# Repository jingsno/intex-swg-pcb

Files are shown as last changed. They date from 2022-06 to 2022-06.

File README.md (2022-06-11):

# Intex SWG automaton

This is a PCB for Intex SWG Automation at
https://github.com/tonyflores1006/intex-swg-iot

Discussion here
https://www.troublefreepool.com/threads/automation-of-intex-swg.228606/

This PCB is suitable for both the TM1650 and the PIC16F88 version of the display board.

Software for the "non TM1650" (18 pin) version of the display board is under development.
(Current status of non released development version of the software, allows for fullt control of the Intex SWG from a web interface.)

Known models without the TM1650 chip:
* Intex Krystal Clear salt water system® ECO 6220 / CG-26670 (7-led/5 buttons), Max 56800 Liters

*PCB for Intex SWG automation*
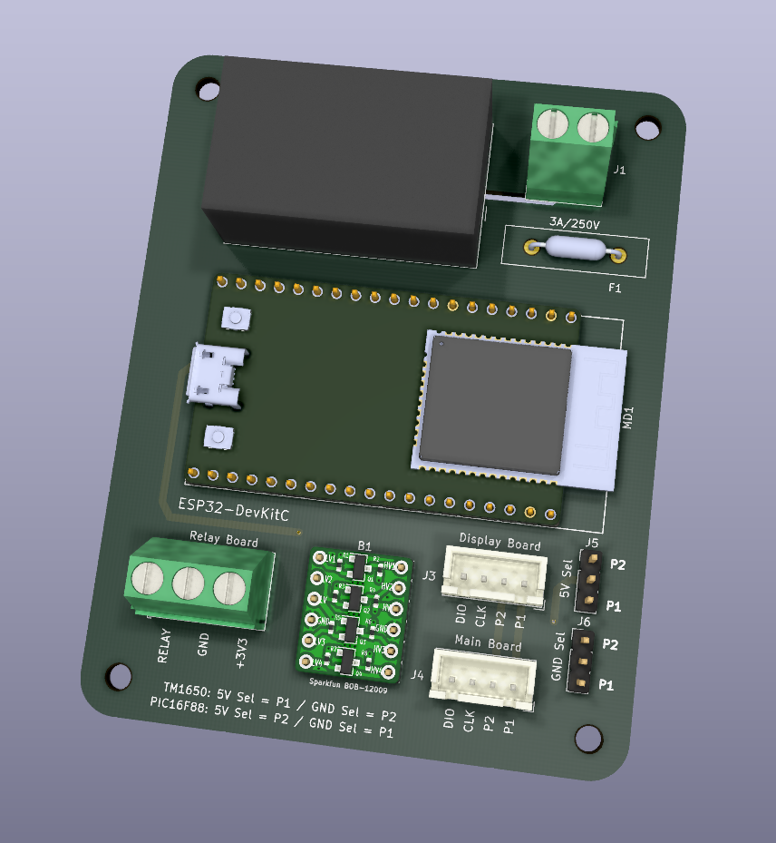
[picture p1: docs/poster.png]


## Schematic

Link to [PDF Schematic](docs/intex-swg-pcb.pdf)

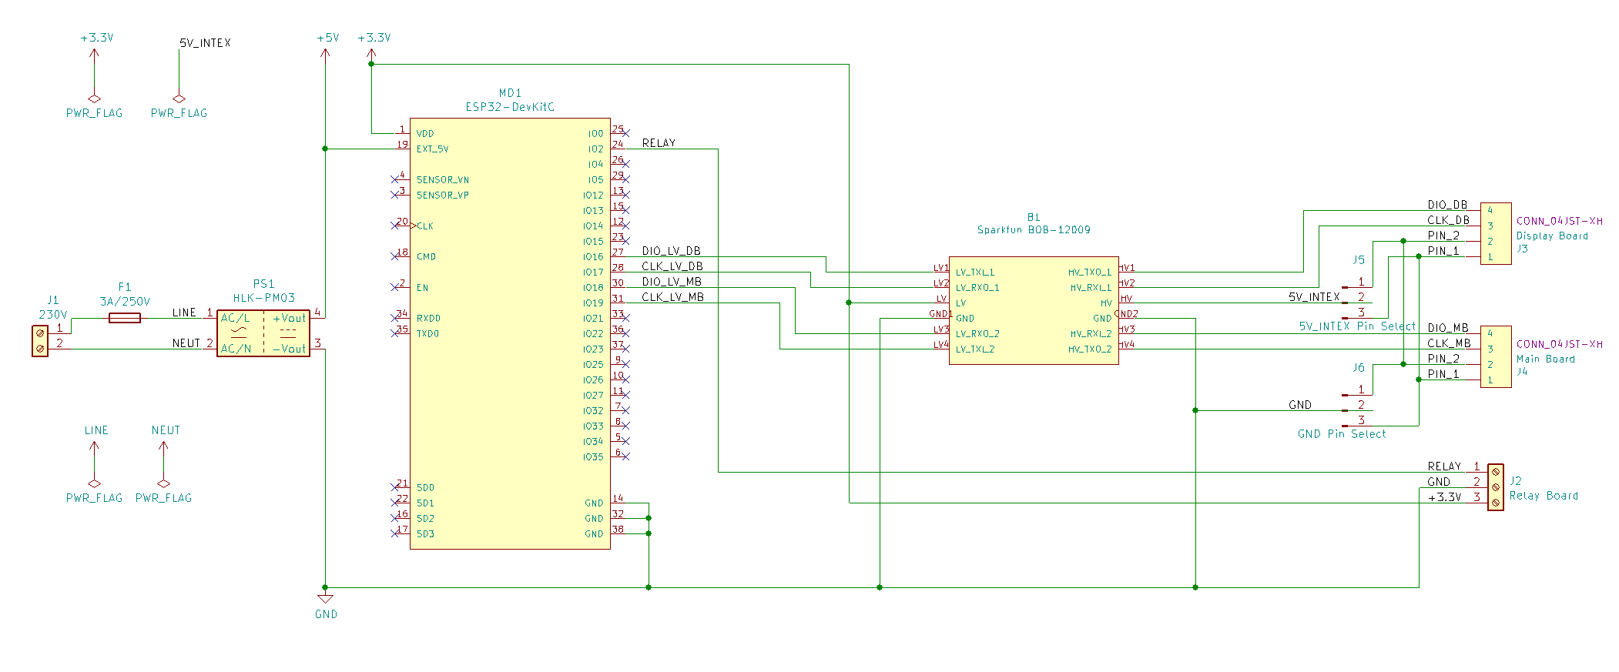
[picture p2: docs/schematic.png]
Schematic


## Parts list

| Part | |
|---|---|
| ESP32-DevkitC ext antenna |  https://www.digikey.com/en/products/detail/espressif-systems/ESP32-DEVKITC-32U/9357002 | 
| IRM-03-5 | https://www.digikey.com/en/products/detail/mean-well-usa-inc/IRM-03-5/7704640 |
| Level shifter to/from 5V/3.3V | https://www.aliexpress.com/item/1005001621978054.html | 
| 3.3V Relay module | https://www.aliexpress.com/item/32884967707.html | 
| 2x Female and 1x Male XH2.54 4pin connectors | https://www.aliexpress.com/item/4000126563819.html | 
| Stepper Motor cables/wire XH2.54 4pin | https://www.aliexpress.com/item/1005001361294507.html |
| Fuse 3A / 250V | https://www.aliexpress.com/item/32702176964.html | 
| 2-pin screw terminal | https://www.aliexpress.com/item/1005002971443405.html  | 
| 3-pin screw terminal | https://www.aliexpress.com/item/1005002971443405.html  | 
| 2x 3-pin header with jumper (or wire) | https://www.aliexpress.com/item/32873263301.html  |

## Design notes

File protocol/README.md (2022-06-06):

# Intex SWG (without TM1650 LED driver) protocol

Some Intex SWG models do not contain the TM1650 LED driver chip
This document contians the protocol for the communication between the Main/Displayboard for these models.

Discussion here
https://www.troublefreepool.com/threads/automation-of-intex-swg.228606/

Known models without the TM1650 chip:
* Intex Krystal Clear salt water system® ECO 6220 / CG-26670 (7-led/5 buttons), Max 56800 Liters

## General signal information

---
#### Note:  The information below is based on the asumption that the encodig is done with a high pulse. This is for decoding purposes. It might also be possible to consider the encoding scheme as "Short-Low,Long-High" as "one. and "Short-Low, Short-High" as Zero. Or alternativly as "Long-High,Short-Low" as "one. and "Short-High,Short-Low, " as Zero

* Starts with a Low 200 μS pulse
* Long High 800 μS for "one", followed by a Low 200 μS pulse as "spacer" 
* Short High 200 μS for "zero", followed by a Low 200 μS pulse as "spacer" 
* Ends with returning to high

---

The communication from the displayboard to the main board (buttons), uses the line marked as "CLK"  
*ESP32: IO17 input from display board, IO19 output to mainboard*

The communication from the main board to the displayboard (7-segment and LEDs), uses the line marked as "DIO"  
*ESP32: IO18 input from main board, IO16 output to displayboard*  

The data lines is normally high  
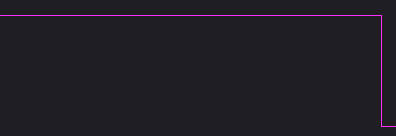
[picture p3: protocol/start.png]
  

A "one" is a long high pulse with the following characteristics:  
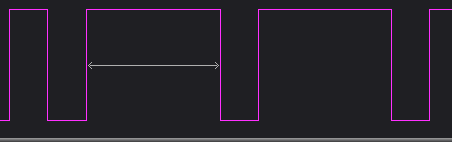
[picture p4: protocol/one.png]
  
Long High 800 μS

A "zero" is a short high pulse with the following characteristics:  
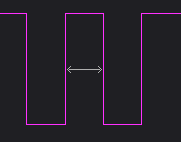
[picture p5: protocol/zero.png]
  
Short High 200 μS

Inbetween the data signals, there is a short low 200μS  
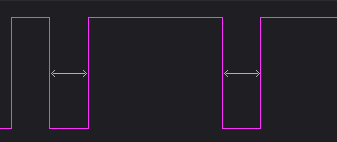
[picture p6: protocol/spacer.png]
  
Short Low 200 μS

The transmission ends with a Short Low of 200μS  
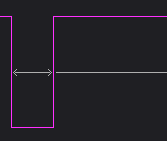
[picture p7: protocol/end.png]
  

## Communication from display board (buttons) to main board

The data from the buttons to the main board consists of two 8 bit values (bytes), where the second byte is the inverted of the first byte

The buttons is arranged in as a "plus", with a center button. They are named N, S, E, W, and C in the following table
~~~
             
             N SCEW  Button pressed  
1111 1011 0000 0100  C 
1111 1101 0000 0010  E 
1111 1110 0000 0001  W 
1110 1111 0001 0000  N 
1111 0111 0000 1000  S 
1111 1100 0000 0011  EW
1110 0111 0001 1000  NS
1110 1110 0001 0001  WN
1111 0110 0000 1001  WS
1110 1101 0001 0010  EN
1111 0101 0000 1010  ES
1111 1111 0000 0000  Release Buttons
---- ---- 
Inverted
of second
byte
~~~

*Example*
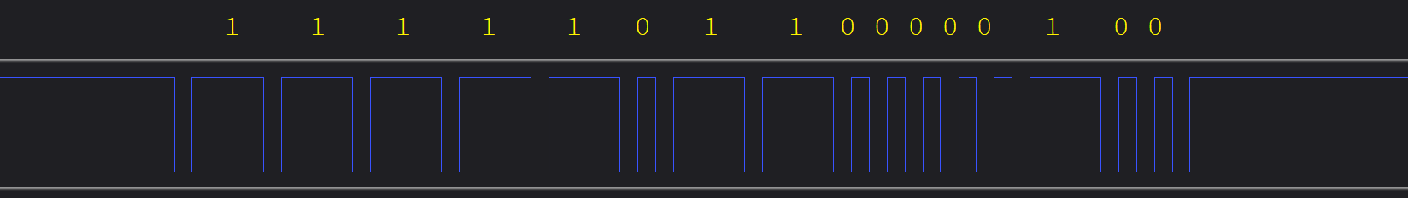
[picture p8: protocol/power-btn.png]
 
*C-button (Power) is pressed*

When the buttons are released the display board transmits
~~~
1111 1111 0000 0000
~~~

On the CG-26670 model, the buttons coresponds to:

N = Boost  
S = Self-Clean  
W = Lock/Unlock  
E = Timer  
C = Power  

## Communication from the main board to display board (7-segment and LEDs)

The data from the main board to the display board (7-segments/and LEDs), consists of a 32 bit value.
The first 16 bits is used for the two 7-segment displays, the last 16 bits for LEDs and status.

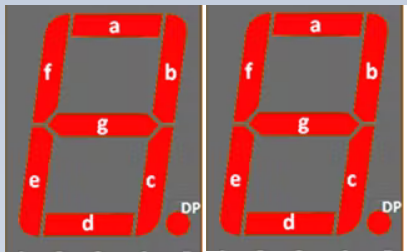
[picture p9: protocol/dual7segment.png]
 

~~~
Left Disp RightDisp 
.gfe dcba .gfe dcba                     Display/LEDs shows
0011 1111 0000 0110 0000 1100 0000 0000 01
0011 1111 0101 1011 0000 1100 0000 0000 02
0000 0110 0011 1111 0000 0100 0000 0000 10
0000 0110 0000 0110 0000 1100 0000 0000 11
0000 0110 0101 1011 0000 1100 0000 0000 12 t0 - "Working" LED On
0000 0110 0101 1011 0000 0100 0000 0000 12 t1 - "Working" LED Off
0000 0110 0101 1011 0000 1100 0000 0000 12 t2 - "Working" LED On
0000 0110 0101 1011 0000 0100 0000 0000 12 t3 - "Working" LED Off
0000 0110 0101 1011 0000 1100 0000 0000 12 t4 - "Working" LED On

0110 1111 0011 1111 0000 0100 0100 0000 90 "Pump Low flow" LED on 
0111 1111 0011 1111 1000 0100 0000 0000 80 "Boost" LED on

1000 0000 0000 0000 0000 0000 0000 0000 Off ("Off", only left "." lights)

Last 16-bits (LED Format):

Left-Disp RightDisp
.gfe dcba .gfe dcba o--s wz-- -pl- --ir
0000 0000 0000 0000 1001 1100 0110 0011 (All 7-segment off, all LEDs on)

o = Boost LED
s = Sleep LED
w = Working LED
z = Ozone LED
p = Pump low flow LED
l = Low salt LED
i = High salt LED
r = Service LED
~~~

There is space for a "Ozone" led on the PCB, not populated on my PCB, that bit is always high when the SWG is powered on, on my SWG.

The mainboard sends the whole 32-bit sequence when blinking LEDs, just toggling the one bit, for the LED thats blinking.

*Example of complete 32-bit display-data sequence*
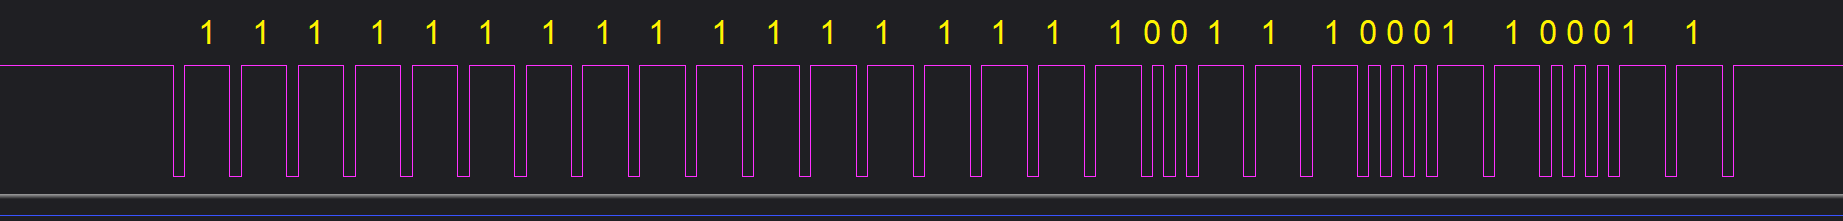
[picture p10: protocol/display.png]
 
*All 7-segments, and LEDs are "on"*

## Power-on
On power-on,  the mainboard sends all 32 bits as "one" to the display board, which lights up everything. One second later, 
it sends all 32 bits as "zero", except the first bit, witch is sendt as "one". This corresponds to just showing the "." in the display.
 
The display boards sends all "Release Button" to the main board, 8 bits of "one", and 8 bits of "zero"

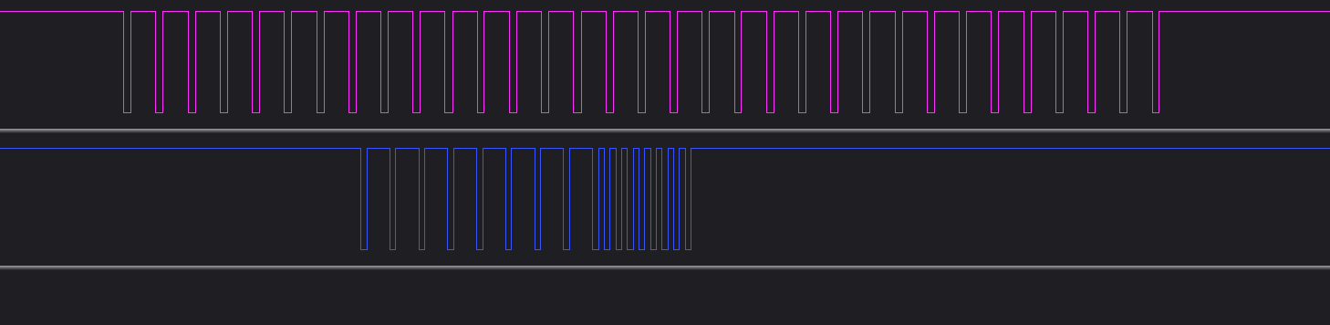
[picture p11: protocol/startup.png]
 

## Code Samples

---
#### Note2: The Code samples below, basically looks for a falling pulse edge, and then measures the time before a falling edge occurs again to detect a "0" or "1"

The following code sample allows the ESP32 to sit "in the middle" between the display and main board. I does not decode the traffic, but prints all rising/falling transitions of the received signals, on the serial bus.  
[Demo_ESP32_Middle](Code/Demo_ESP32_Middle/Demo_ESP32_Middle.ino)

The following code sample allows the ESP32 to send different LED patterns to the display board.  
[Demo_ESP32_Display](Code/Demo_ESP32_Display/Demo_ESP32_Display.ino)

The following code sample allows the ESP32 to DEMO the following sequernce: Push the Power button, Push the Lock/Unlock Key, Push the Timer button 6-times, Push the Lock/Unlock Key, and at last Push the power Button. Repeats the sequence after 10 Seconds  (Includes some Demo_ESP32_Middle code to allow the SWG to work)  
[Demo_ESP32_Buttons](Code/Demo_ESP32_Buttons/Demo_ESP32_Buttons.ino)

The following code sample allows the ESP32 to read, and print on the serial bus, the buttons pressed on the display board (Includes some Demo_ESP32_Middle code to allow the SWG to work)  
[Demo_ESP32_ReadButtons](Code/Demo_ESP32_ReadButtons/Demo_ESP32_Buttons.ino)

The following code sample allows the ESP32 to read, and print on the serial bus, the information sendt from the main board to the display board (Includes some Demo_ESP32_Middle code to allow the SWG to work)  
[Demo_ESP32_ReadDisplay](Code/Demo_ESP32_ReadDisplay/Demo_ESP32_ReadDisplay.ino)

The following code sample uses code from all the above samples, to decode and display all data between the main board and the displayboard  
[Demo_ESP32](Code/Demo_ESP32/Demo_ESP32.ino)

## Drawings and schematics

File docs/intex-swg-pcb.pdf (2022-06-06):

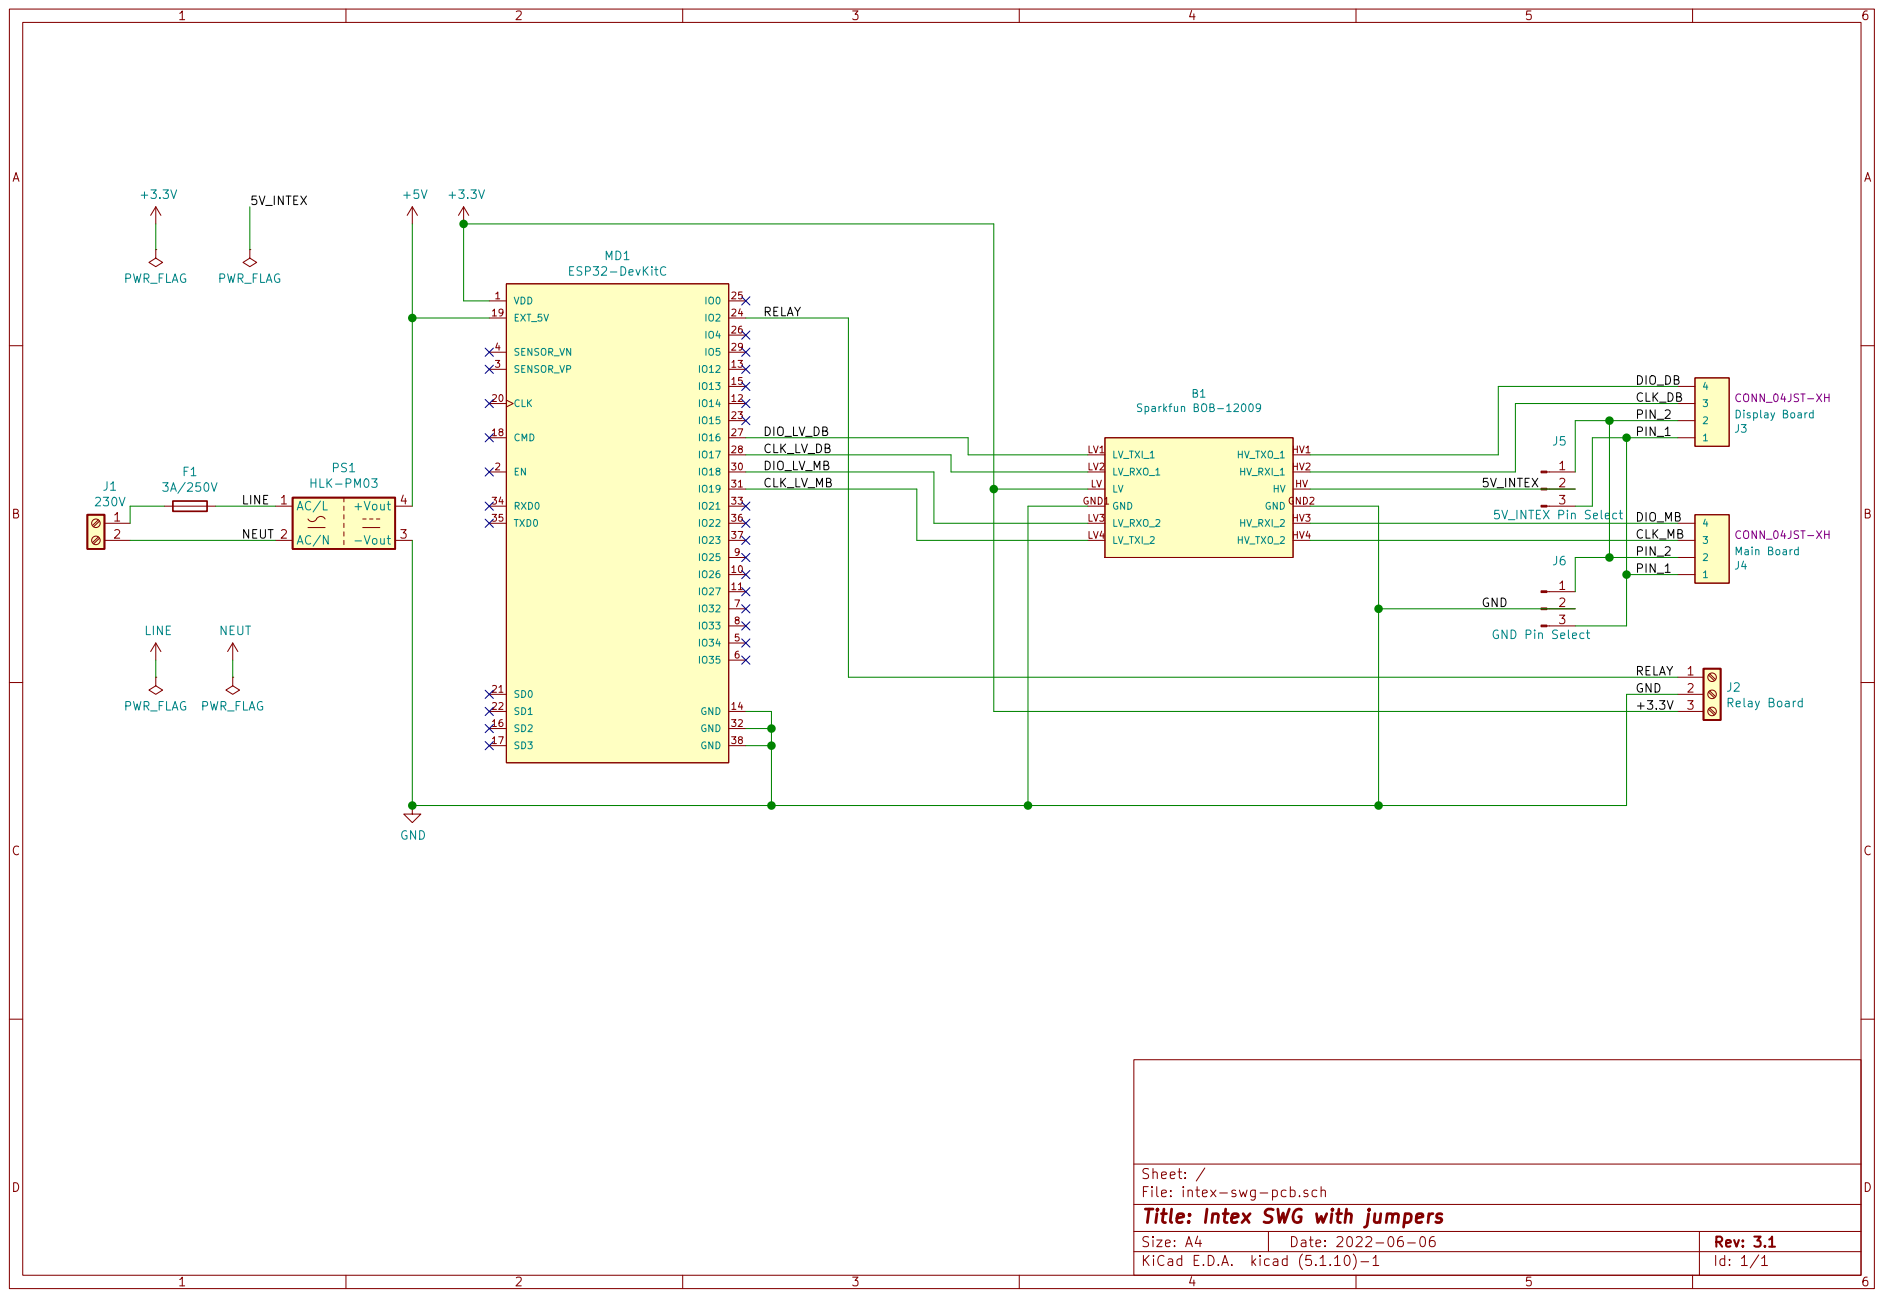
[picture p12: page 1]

J6 GND Pin Select GND

File: intex-swg-pcb.sch Sheet: /
Id: 1/1 Title: Intex SWG with jumpers

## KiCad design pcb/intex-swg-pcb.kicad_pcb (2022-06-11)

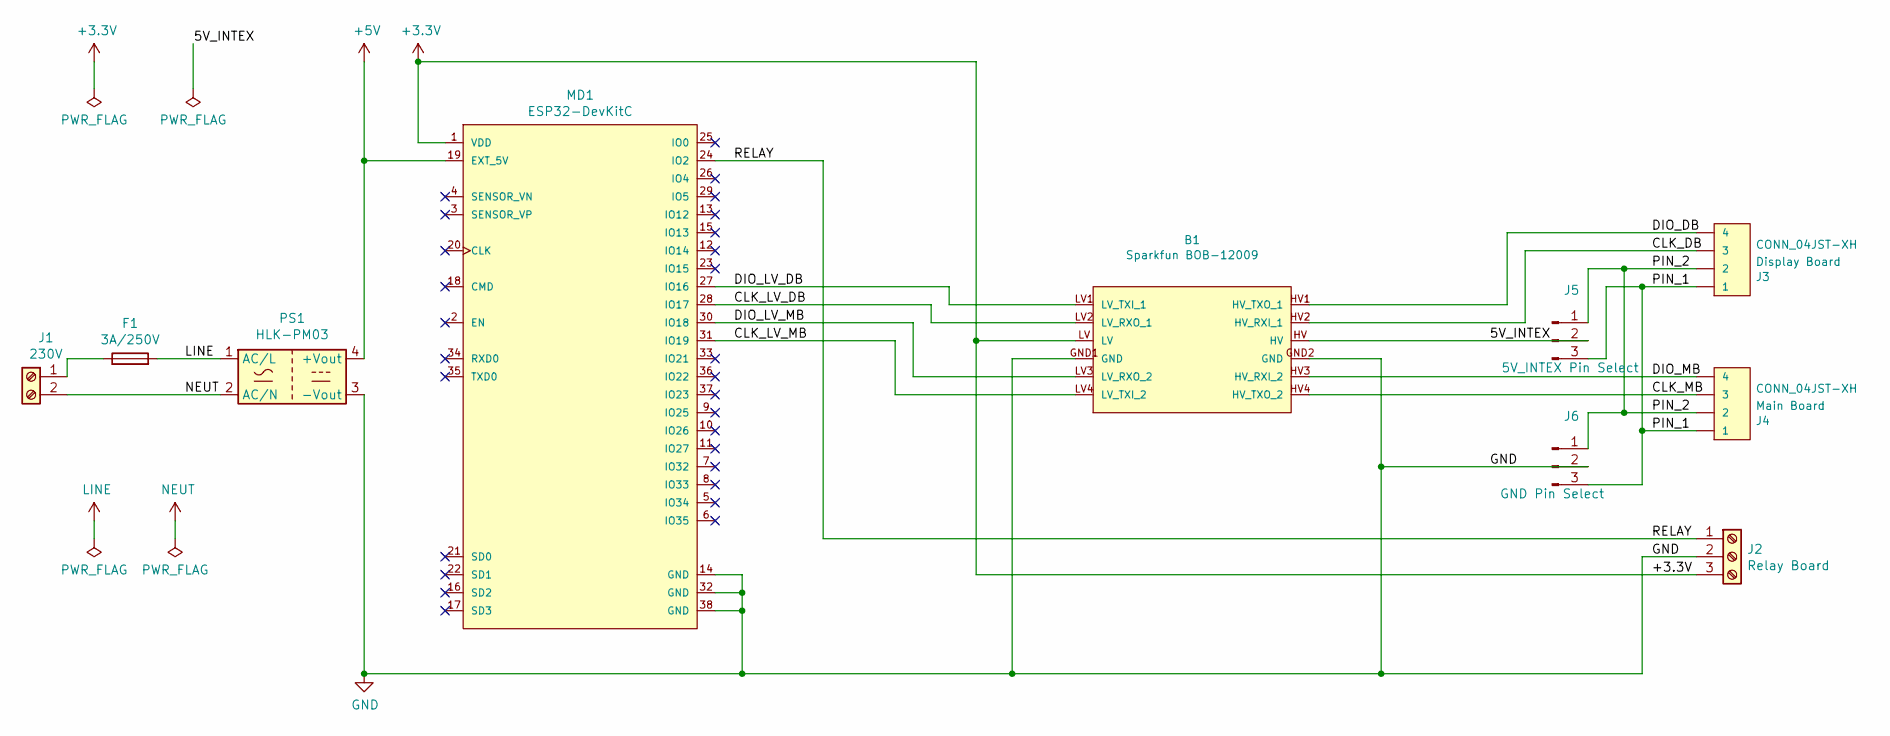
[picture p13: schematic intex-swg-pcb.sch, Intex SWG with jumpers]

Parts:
B1: Sparkfun BOB-12009; SPARKFUN_LOGIC_LEVEL_CONVERTER; digi-key part number 1568-1209-ND
F1: 3A/250V; Fuse_Littelfuse-LVR100
J1: 230V; TerminalBlock_Phoenix_MKDS-1,5-2_1x02_P5.00mm_Horizontal
J2: Relay Board; TerminalBlock_Phoenix_MKDS-1,5-3_1x03_P5.00mm_Horizontal
J3: Display Board; JST_XH_B4B-XH-A_1x04_P2.50mm_Vertical; digi-key part number 455-2249-ND
J4: Main Board; JST_XH_B4B-XH-A_1x04_P2.50mm_Vertical; digi-key part number 455-2249-ND
J5: 5V_INTEX Pin Select; PinHeader_1x03_P2.54mm_Vertical
J6: GND Pin Select; PinHeader_1x03_P2.54mm_Vertical
MD1: ESP32-DevKitC; Espressif-ESP32-DevKitC_V4-0-0-MFG; mouser part number 356-ESP32-DEVKITC
PS1: HLK-PM03; Converter_ACDC_HiLink_HLK-PMxx

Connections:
+3V3: B1.LV, J2.3, MD1.1 (VDD)
+5V: MD1.19 (EXT_5V), PS1.4 (+Vout)
/5V_INTEX: B1.HV, J5.2
/CLK_DB: B1.HV2 (HV_RXI_1), J3.3
/CLK_LV_DB: B1.LV2 (LV_RXO_1), MD1.28 (IO17)
/CLK_LV_MB: B1.LV4 (LV_TXI_2), MD1.31 (IO19)
/CLK_MB: B1.HV4 (HV_TXO_2), J4.3
/DIO_DB: B1.HV1 (HV_TXO_1), J3.4
/DIO_LV_DB: B1.LV1 (LV_TXI_1), MD1.27 (IO16)
/DIO_LV_MB: B1.LV3 (LV_RXO_2), MD1.30 (IO18)
/DIO_MB: B1.HV3 (HV_RXI_2), J4.4
/PIN_1: J3.1, J4.1, J5.3, J6.3
/PIN_2: J3.2, J4.2, J5.1, J6.1
/RELAY: J2.1, MD1.24 (IO2)
GND: B1.GND1 (GND), B1.GND2 (GND), J2.2, J6.2, MD1.14 (GND), MD1.32 (GND), MD1.38 (GND), PS1.3 (-Vout)
LINE: F1.2, PS1.1 (AC/L)
NEUT: J1.2, PS1.2 (AC/N)
unnamed: F1.1, J1.1

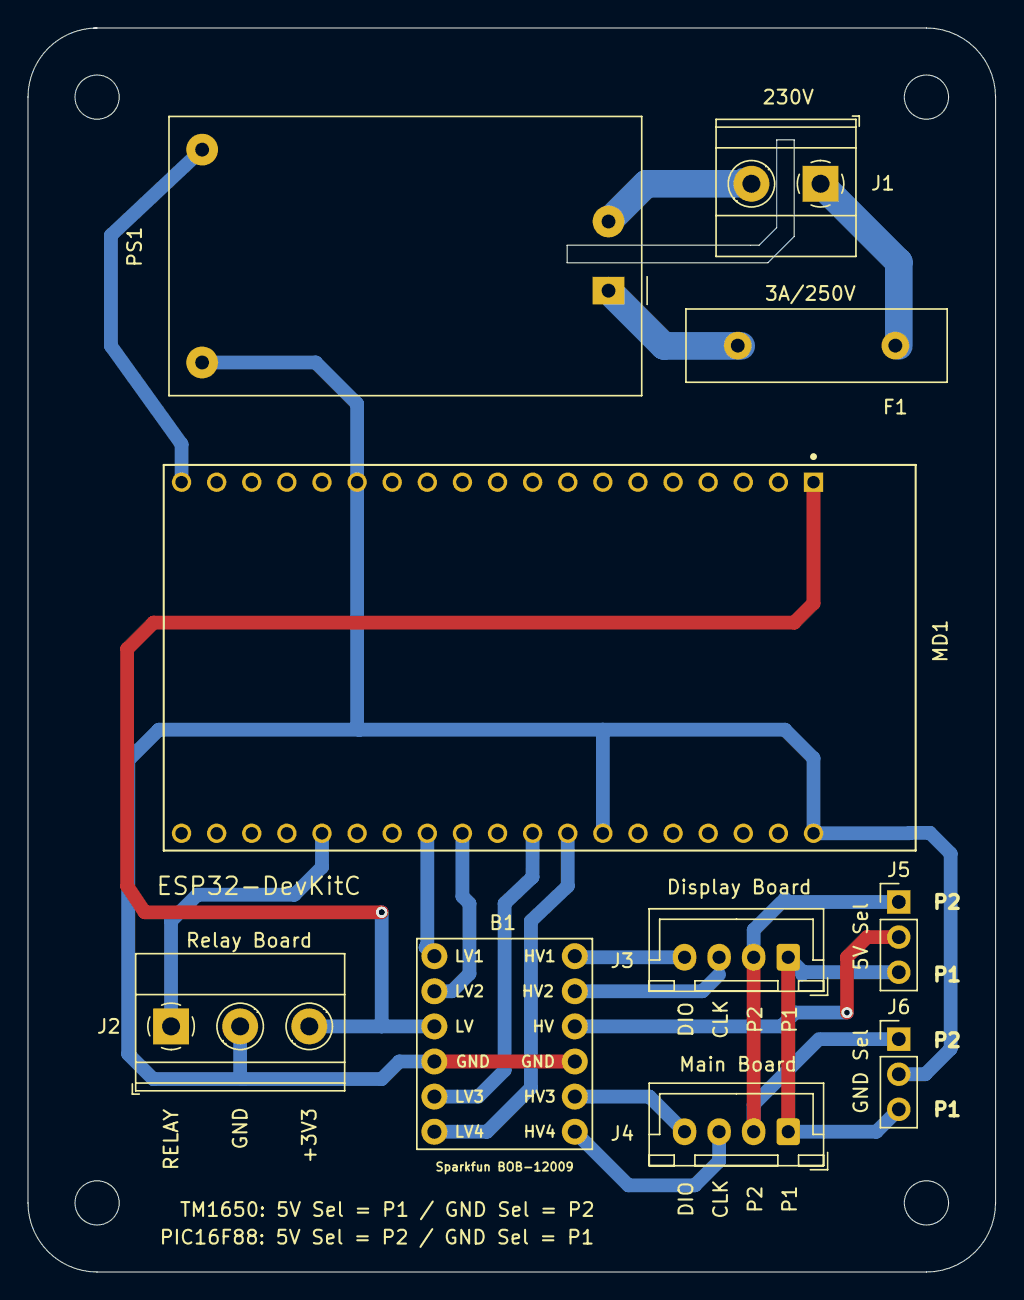
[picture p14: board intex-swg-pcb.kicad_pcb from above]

Board: 2 copper layers, 70.0 x 90.0 mm, 10 parts (0 on the bottom side), 18 nets.

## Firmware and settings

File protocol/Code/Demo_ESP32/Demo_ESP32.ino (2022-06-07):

// Define all I/O pins
#define FROM_DISP 17
#define TO_DISP 16
#define FROM_MAIN 18
#define TO_MAIN 19
#define RELAY 2

// Define Buttons
#define DEBOUNCE              50 // 50mS delay before releasing buttons
#define BUTTON_BOOST        0x10 // 0b11101111 00010000 (The first 8 inverted bits are generated in the subroutine)
#define BUTTON_TIMER        0x02 // 0b11111101 00000010 (The first 8 inverted bits are generated in the subroutine)
#define BUTTON_POWER        0x04 // 0b11111011 00000100 (The first 8 inverted bits are generated in the subroutine)
#define BUTTON_LOCK         0x01 // 0b11111110 00000001 (The first 8 inverted bits are generated in the subroutine)
#define BUTTON_SELF_CLEAN   0x08 // 0b11110111 00001000 (The first 8 inverted bits are generated in the subroutine)
#define BUTTON_RELEASE      0x00 // 0b11111111 00000000 (The first 8 inverted bits are generated in the subroutine)

// Define LEDs
#define LED_OZONE           0x400  // 0b00000000 00000000 00000100 00000000
#define LED_SLEEP           0x1000 // 0b00000000 00000000 00010000 00000000
#define LED_BOOST           0x8000 // 0b00000000 00000000 10000000 00000000
#define LED_POWER           0x800  // 0b00000000 00000000 00001000 00000000
#define LED_PUMP_LOW_FLOW   0x40   // 0b00000000 00000000 00000000 01000000
#define LED_LOW_SALT        0x20   // 0b00000000 00000000 00000000 00100000
#define LED_HIGH_SALT       0x2    // 0b00000000 00000000 00000000 00000010
#define LED_SERVICE         0x1    // 0b00000000 00000000 00000000 00000001

// Segment-bit: DP G F E D C B A
#define DISP_BLANK  0b00000000
#define DISP_0      0b00111111
#define DISP_1      0b00000110
#define DISP_2      0b01011011
#define DISP_3      0b01001111
#define DISP_4      0b01100110
#define DISP_5      0b01101101
#define DISP_6      0b01111101
#define DISP_7      0b00000111
#define DISP_8      0b01111111
#define DISP_9      0b01101111
#define DISP_DP     0b10000000
#define DISP_A      0b01110111
#define DISP_P      0b01110011
#define DISP_1_CLEAN_06P 0b11111101 // Right Disp, My SWG does not show "." in right display when in clean mode
#define DISP_1_CLEAN_10P 0b10111111 // Right Disp, My SWG does not show "." in right display when in clean mode
#define DISP_1_CLEAN_14P 0b11100110 // Right Disp, My SWG does not show "." in right display when in clean mode

// Define pulse lengts
const unsigned long bit1_MIN = 800;
const unsigned long bit1_MAX = 1200;
const unsigned long bit0_MIN = 200;
const unsigned long bit0_MAX = 600;

// Interrupt variables
unsigned long fall_Time_isr0 = 0;       // isr0 placeholder for microsecond time when last falling edge occured.
unsigned long rise_Time_isr0 = 0;       // isr0 placeholder for microsecond time when last rising edge occured.

unsigned long fall_Time_isr1 = 0;       // isr1 placeholder for microsecond time when last falling edge occured.
unsigned long rise_Time_isr1 = 0;       // isr1 placeholder for microsecond time when last rising edge occured.

int relay_state = LOW;  // the current state of relay

int i_isr0;
int i_isr1;

word tmpdisplaydata;
word tmpinputbutton;
word displaydata = 0x0;
word inputbutton = 0x0;

void setup() {
  // put your setup code here, to run once:
  Serial.begin(115200);

  Serial.println(F("SETUP: MAIN_BOARD -> ESP32 -> DISPLAY_BOARD"));
  pinMode(FROM_MAIN,INPUT); // Receive data from main board
  Serial.println(F("FROM_MAIN (Pin 18) Configured for input from main board."));
  attachInterrupt(FROM_MAIN,PinChangeISR0,CHANGE);
  Serial.println(F("FROM_MAIN (Pin 18) ISR0 function attached."));

  pinMode(TO_DISP,OUTPUT);  // Send data to display board
  digitalWrite(TO_DISP, HIGH); // sets the TO_DISP signal to HIGH
  Serial.println(F("TO_DISP   (Pin 16) Configured for output to display board."));

  Serial.println();

  Serial.println(F("SETUP: DISPLAY_BOARD -> ESP32 -> MAIN_BOARD"));
  pinMode(FROM_DISP,INPUT); // Receive data from display board
  Serial.println(F("FROM_DISP (Pin 17) Configured for input from display board."));
  attachInterrupt(17,PinChangeISR1,CHANGE);
  Serial.println(F("FROM_DISP (Pin 17) ISR1 function attached."));
 
  pinMode(TO_MAIN,OUTPUT); // Send data to main board
  digitalWrite(TO_MAIN, HIGH); // sets the TO_MAIN signal to HIGH
  Serial.println(F("TO_MAIN   (Pin 19) Configured for output to main board."));

  Serial.println();

  Serial.println(F("[Self-Clean]+[Boost] will toggle relay"));

  // Configures relay, and sets it to low/off
  pinMode(RELAY, OUTPUT); 
  digitalWrite(RELAY, LOW);
  
}

void loop() {

// We do nothing here!

}

// Interupt routine; read data from mainboard. Triggers on "FROM_MAIN" pin change
void PinChangeISR0(){                                     // Pin FROM_MAIN (Interrupt 0) service routine
  unsigned long Time_isr0 = micros();                     // Get current time
  
  if (digitalRead(FROM_MAIN) == LOW) {
    // Falling edge
    digitalWrite(TO_DISP,LOW);

      Time_isr0 = micros() - fall_Time_isr0;              // Subtract last falling edge to get pulse time.

        // Looking for Data
        if ((Time_isr0 > bit0_MIN) && (Time_isr0 < bit0_MAX)) {
          // 0 bit
          bitWrite(displaydata,i_isr0,0);
          i_isr0++;
        }
        else if ((Time_isr0 > bit1_MIN) && (Time_isr0 < bit1_MAX)) {
          // 1 bit
          bitWrite(displaydata,i_isr0,1);
          i_isr0++;
        }
        else {
          // Not a 0 or 1 bit so restart data build
          i_isr0=0;
          displaydata=0x0;
        }

        // Do we have a complete bitstream?
        if (i_isr0 >= 32) {
            // We're still in the interupt code, so we also need to set a global variable, and notify the main code
            // that we've have display data
           
              tmpdisplaydata=0x0;
              
              // Loops through the 32-bit value, from left to right, reverses the bit order
              for(int i = 0, mask = 0x80000000; i < 32; i++, mask = (word)mask >> 1)
              {
                  if (displaydata & mask) 
                  {
                    bitWrite(tmpdisplaydata,i,1);         
                  }
                  else
                  {
                    bitWrite(tmpdisplaydata,i,0);      
                  }
               }

               displaydata = tmpdisplaydata;
           
            // Get left digit   
            unsigned int LEFT_DIGIT = (unsigned int)displaydata >> 24;
                       
            // Get right digit
            unsigned int RIGHT_DIGIT =(unsigned int)displaydata >> 16;
            RIGHT_DIGIT =(unsigned int)RIGHT_DIGIT << 8;
            RIGHT_DIGIT =(unsigned int)RIGHT_DIGIT >> 8;

            // Print LED display
            Serial.print(" [");
            Serial.print(getDisplayDigitFromCode( LEFT_DIGIT & 0b01111111));  // Left 7-segment
            Serial.print(getDisplayDigitFromCode( LEFT_DIGIT & DISP_DP));     // Left .
            Serial.print(getDisplayDigitFromCode( RIGHT_DIGIT & 0b01111111)); // Right 7-segment
            Serial.print(getDisplayDigitFromCode( RIGHT_DIGIT & DISP_DP));    // Right .
            Serial.print("]");

            // Print Status LEDs
            Serial.print(" LED: ");
            if (displaydata & LED_POWER)        { Serial.print("POWER=ON  "); } else { Serial.print("POWER=OFF "); }
            if (displaydata & LED_SLEEP)        { Serial.print("SLEEP=ON  "); } else { Serial.print("SLEEP=OFF "); }
            if (displaydata & LED_PUMP_LOW_FLOW){ Serial.print("PUMP_LOW_FLOW=ON  "); } else { Serial.print("PUMP_LOW_FLOW=OFF "); }
            if (displaydata & LED_LOW_SALT)     { Serial.print("LOW_SALT=ON  "); } else { Serial.print("LOW_SALT=OFF "); }
            if (displaydata & LED_HIGH_SALT)    { Serial.print("HIGH_SALT=ON  "); } else { Serial.print("HIGH_SALT=OFF "); }            
            if (displaydata & LED_BOOST)        { Serial.print("BOOST=ON  "); } else { Serial.print("BOOST=OFF "); }
            if (displaydata & LED_SERVICE)      { Serial.print("SERVICE=ON  "); } else { Serial.print("SERVICE=OFF "); }
            if (displaydata & LED_OZONE)        { Serial.print("OZONE=ON  "); } else { Serial.print("OZONE=OFF "); }

            Serial.print(" ");
            Serial.println(displaydata,HEX);
        }

      fall_Time_isr0 = micros();                               // Store fall time

  }
  else {
    // Rising edge
    digitalWrite(TO_DISP,HIGH);
    rise_Time_isr0 = Time_isr0;                                   // Store rise time
  }
}


// Interupt routine; read data from display. Triggers on "FROM_DISP" pin change
void PinChangeISR1(){                                     // Pin FROM_DISP (Interrupt 1) service routine
  unsigned long Time_isr1 = micros();                          // Get current time
  
  if (digitalRead(FROM_DISP) == LOW) {
    // Falling edge
    digitalWrite(TO_MAIN,LOW);

      Time_isr1 = micros() - fall_Time_isr1;                        // Subtract last falling edge to get pulse time.

        // Looking for Data
        if ((Time_isr1 > bit0_MIN) && (Time_isr1 < bit0_MAX)) {
          // 0 bit
          bitWrite(inputbutton,i_isr1,0);
          i_isr1++;
        }
        else if ((Time_isr1 > bit1_MIN) && (Time_isr1 < bit1_MAX)) {
          // 1 bit
          bitWrite(inputbutton,i_isr1,1);
          i_isr1++;
        }
        else {
          // Not a 0 or 1 bit so restart data build
          i_isr1=0;
          inputbutton=0x0;
        }

        // Do we have a complete bitstream?
        if (i_isr1 >= 16) {

            // We're still in the interupt code, so we also need to set a global variable, and notify the main code
            // that we've have a button press

              tmpinputbutton=0x0;
              
              // Loops through the 16-bit value, from left to right, reverses the bit order
              for(int i = 0, mask = 0x8000; i < 16; i++, mask = (word)mask >> 1)
              {
                  if (inputbutton & mask) 
                  {
                    bitWrite(tmpinputbutton,i,1);         
                  }
                  else
                  {
                    bitWrite(tmpinputbutton,i,0);      
                  }
               }

            // Strip first 8 bits
            inputbutton = ((int)tmpinputbutton & 0b11111111);

            if (inputbutton & BUTTON_LOCK)       {Serial.print("[Lock]"); }
            if (inputbutton & BUTTON_TIMER)      {Serial.print("[Timer]"); }
            if (inputbutton & BUTTON_POWER)      {Serial.print("[Power]"); }
            if (inputbutton & BUTTON_SELF_CLEAN) {Serial.print("[Self-Clean]");}
            if (inputbutton & BUTTON_BOOST)      {Serial.print("[Boost]"); }
            if (inputbutton & (BUTTON_LOCK | BUTTON_TIMER | BUTTON_POWER | BUTTON_SELF_CLEAN | BUTTON_BOOST)) { Serial.println(); }

            if (inputbutton == BUTTON_RELEASE)    {Serial.println("[Button Release]"); }
            
            // Toggle relay ?
            if ((inputbutton & BUTTON_SELF_CLEAN) && (inputbutton & BUTTON_BOOST)) {Serial.println("[RELAY TOGGLE]");  relay_state = !relay_state;}
            digitalWrite(RELAY, relay_state);
}

      fall_Time_isr1 = micros();                               // Store fall time

  }
  else {
    // Rising edge
    digitalWrite(TO_MAIN,HIGH);
    rise_Time_isr1 = Time_isr1;                                   // Store rise time
  }
}

char getDisplayDigitFromCode(uint8_t code) {
    switch (code) {
        case DISP_BLANK:  return ' ';
        case DISP_0: return '0';
        case DISP_1: return '1';
        case DISP_2: return '2';
        case DISP_3: return '3';
        case DISP_4: return '4';
        case DISP_5: return '5';
        case DISP_6: return '6';
        case DISP_7: return '7';
        case DISP_8: return '8';
        case DISP_9: return '9';
        case DISP_DP: return '.';
        case DISP_1_CLEAN_06P: return '6';
        case DISP_1_CLEAN_10P: return '0';
        case DISP_1_CLEAN_14P: return '4';
        default: return 0;
    }
}

void SerialPrintZeroPad32bit(int var) {
  for (unsigned int test = 0x80000000; test; test >>= 1) {
    Serial.write(var  & test ? '1' : '0');
  }
}

void SerialPrintZeroPad16bit(int var) {
  for (unsigned int test = 0x8000; test; test >>= 1) {
    Serial.write(var  & test ? '1' : '0');
  }
}


void SerialPrintZeroPad8bit(int var) {
  for (unsigned int test = 0x80; test; test >>= 1) {
    Serial.write(var  & test ? '1' : '0');
  }
}

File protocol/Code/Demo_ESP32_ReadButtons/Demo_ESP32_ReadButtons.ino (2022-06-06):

// Define all I/O pins
#define FROM_DISP 17
#define TO_DISP 16
#define FROM_MAIN 18
#define TO_MAIN 19
#define RELAY 0

// Define Buttons
#define DEBOUNCE              50 // 50mS delay before releasing buttons
#define BUTTON_BOOST        0x10 // 0b1110111100010000 (The first 8 inverted bits are generated in the subroutine)
#define BUTTON_TIMER        0x02 // 0b1111110100000010 (The first 8 inverted bits are generated in the subroutine)
#define BUTTON_POWER        0x04 // 0b1111101100000100 (The first 8 inverted bits are generated in the subroutine)
#define BUTTON_LOCK         0x01 // 0b1111111000000001 (The first 8 inverted bits are generated in the subroutine)
#define BUTTON_SELF_CLEAN   0x08 // 0b1111011100001000 (The first 8 inverted bits are generated in the subroutine)
#define BUTTON_RELEASE      0x00 // 0b1111111100000000 (The first 8 inverted bits are generated in the subroutine)

// Constants
const unsigned long bit1_MIN = 800;
const unsigned long bit1_MAX = 1200;
const unsigned long bit0_MIN = 200;
const unsigned long bit0_MAX = 600;

// Interrupt variables
unsigned long fall_Time_isr0 = 0;       // Placeholder for microsecond time when last falling edge occured.
unsigned long rise_Time_isr0 = 0;       // Placeholder for microsecond time when last rising edge occured.
unsigned long fall_Time_isr1 = 0;       // Placeholder for microsecond time when last falling edge occured.
unsigned long rise_Time_isr1 = 0;       // Placeholder for microsecond time when last rising edge occured.

int i_isr1;
word inputbutton = 0x0;

void setup() {
  // put your setup code here, to run once:
  Serial.begin(115200);

  pinMode(FROM_MAIN,INPUT); // Receive data from main board
  Serial.println(F("FROM_MAIN (Pin 18) Configured for main board input."));
  attachInterrupt(FROM_MAIN,PinChangeISR0,CHANGE);
  Serial.println(F("FROM_MAIN (Pin 18) ISR0 function attached."));
  pinMode(TO_DISP,OUTPUT);  // Send data to display board
  Serial.println(F("TO_DISP (Pin 16) Configured for display board output."));
  
  pinMode(FROM_DISP,INPUT); // Receive data from display board
  Serial.println(F("FROM_DISP (Pin 17) Configured for display board input."));
  attachInterrupt(17,PinChangeISR1,CHANGE);
  Serial.println(F("FROM_DISP (Pin 17) ISR1 function attached."));
  pinMode(TO_MAIN,OUTPUT); // Send data to main board
  Serial.println(F("TO_MAIN (Pin 19) Configured for main board output."));

  digitalWrite(TO_DISP, HIGH); // sets the TO_DISP signal to HIGH
  digitalWrite(TO_MAIN, HIGH); // sets the TO_MAIN signal to HIGH
}

void loop() {

}

void PinChangeISR0(){                                     // Pin FROM_MAIN (Interrupt 0) service routine
  if (digitalRead(FROM_MAIN) == LOW) {
    // Falling edge
    digitalWrite(TO_DISP,LOW);
    //for debugging
    //Serial.print("f");
  }
 
  else {
    // Rising edge
    digitalWrite(TO_DISP,HIGH);                             // Transmit to display
    //for debugging
    //Serial.print("r");
  }
}


void PinChangeISR1(){                                     // Pin FROM_DISP (Interrupt 1) service routine
  unsigned long Time_isr1 = micros();                          // Get current time
  
  if (digitalRead(FROM_DISP) == LOW) {
    // Falling edge
    digitalWrite(TO_MAIN,LOW);

      Time_isr1 = micros() - fall_Time_isr1;                        // Subtract last falling edge to get pulse time.

        // Looking for Data
        if ((Time_isr1 > bit0_MIN) && (Time_isr1 < bit0_MAX)) {
          // 0 bit
          bitWrite(inputbutton,i_isr1,0);
          i_isr1++;
          //for debugging
          //Serial.print("0");
          //for debugging. NOTE breaks code due to too mutch data to serial
          //Serial.print("Pulse Time: ");
          //Serial.println(Time);            
        }
        else if ((Time_isr1 > bit1_MIN) && (Time_isr1 < bit1_MAX)) {
          // 1 bit
          bitWrite(inputbutton,i_isr1,1);
          i_isr1++;
          //for debugging
          //Serial.print("1");
          //for debugging. NOTE breaks code due to too mutch data to serial
          //Serial.print("Pulse Time: ");
          //Serial.println(Time);            
        }
        else {
          // Not a 0 or 1 bit so restart data build

          //for debugging
          //Serial.println();
          //Serial.print("?");
          //Serial.println();          
          //for debugging. NOTE breaks code due to too mutch data to serial
          //Serial.print("Pulse Time: ");
          //Serial.println(Time);   
          
          i_isr1=0;
          inputbutton=0x0;
        }

        if (i_isr1 >= 16) {
            // Ok! Here we really need to reverse the bit order of the inputbutton variable, strip away the first byte, 
            // and we are left with the button values in the declarations. 
            // But I've spendt to much time on this, so I'll just do somehing quick and dirty, for demo purposes
            // We're still in the interupt code, so we also need to set a global variable, and notify the main code
            // that we've have a button press

              word tmpinputbutton;
              // Loops through the 16-bit value, from left to right, reverses the bit order
              for(int i = 0, mask = 0x8000; i < 16; i++, mask = (word)mask >> 1)
              {
                  if (inputbutton & mask) 
                  {
                    bitWrite(tmpinputbutton,i,1);         
                  }
                  else
                  {
                    bitWrite(tmpinputbutton,i,0);      
                  }
               }

            inputbutton = tmpinputbutton;
           
            //Serial print binary value with zero padding
            //SerialPrintZeroPad8bit((int)inputbutton & 0b11111111);
            //Serial.print(" "); 
           
            switch ((int)inputbutton & 0b11111111) {
              case BUTTON_LOCK: // Lock
                Serial.println("[Lock]");
                break;
              case BUTTON_TIMER: // Timer
                Serial.println("[Timer]");
                break;
              case BUTTON_POWER: // Power
                Serial.println("[Power]");
                break;
              case BUTTON_SELF_CLEAN: // Self-Clean
                Serial.println("[Self-Clean]");
                break;
              case BUTTON_BOOST: // Boost
                Serial.println("[Boost]");
                break;               
              case BUTTON_RELEASE: // Button Releaset
                Serial.println("[Button Release]");               
                break;
              default:
                break;
            }
}

      //for debugging       
      //Serial.print(F("F"));
      fall_Time_isr1 = micros();                               // Store fall time

  }
  else {
    // Rising edge
    digitalWrite(TO_MAIN,HIGH);
    rise_Time_isr1 = Time_isr1;                                   // Store rise time
   //for debugging
   //Serial.print(F("R"));
  }
}
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

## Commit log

2022-05-22 Removed non updated BOM files
2022-06-06 Swapped relay to GPIO2
    [intex-swg-pcb.kicad_pcb, intex-swg-pcb.sch]
2022-06-06 Uploaded protocol documentation/code samples
2022-06-06 Set datalines high on ESP32 boot
2022-06-07 Clean, fixed, and expanded Demo_ESP32 code
    [Demo_ESP32.ino]
2022-06-11 Corrected top left mounting hole, that was 0.24mm offset
    [intex-swg-pcb.kicad_pcb]
